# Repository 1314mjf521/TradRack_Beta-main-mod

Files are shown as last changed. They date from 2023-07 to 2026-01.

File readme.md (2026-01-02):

<!--
 * @Author: Mjf
 * @Date: 2023-06-24 20:04:52
 * @LastEditTime: 2024-05-12 15:53:49
 * @LastEditors: Win_VScode
 * @Description: 
 * @FilePath: \undefinedf:\download\TradRack_Beta-main\STLs\TradRack_Beta-main-mod\TradRack_Beta-main-mod\readme.md
 * 版权声明暂无
-->
# 以上MOD文件仅为测试使用用途，不得进行商用，不得进行商用，同时文件为开放式下载可进行转发及Fork但是不得商用售卖，一经发现拉黑，通告处理，源文件作者保留相关知识产权及法律诉讼通道，将提供文件归属权及开放时间证明！
## 仅仅是MOD文件不做解释全中文注释，有英文啥的不知道是啥随便看吧！  

# 本仓库仅为MOD文件不是完整文件，需要完整文件的自行找作者更新不解释原因  

中文TR-MOD解释用啥英文不可能得！！  

全套MOD不负责进行解释，搜集整理不会用别问我都是群友的自己去兔子群下载，高速下载衔接懒得放心情好了我在放！  
注意！！  
    在个别MOD文件中会有多个压缩文件，由于文件大小限制必须使用100M以下文件，所以进行打包！、

[TR公测地址](https://github.com/Annex-Engineering/TradRack)  
[TR开源衔接-国内加速](https://gitee.com/mjf521/TradRack)  
[动态网床使用-耗爹油](https://github.com/eamars/klipper_adaptive_bed_mesh)  
[动态网床使用-耗爹油-国内加速衔接](https://gitee.com/mjf521/klipper_adaptive_bed_mesh.git)  
[兔子垂直料架开源-耗爹油](https://github.com/eamars/VoronPrinterMods/tree/main/ercf_vertical_extrusion_stand)  
[兔子垂直料架开源-耗爹油-国内加速衔接](https://gitee.com/mjf521/VoronPrinterMods.git)  
[四色换色开源-唔，待定](https://github.com/feiwtyro/FEIW-multi_color)  
[四色换色开源-唔，待定-国内加速衔接](https://gitee.com/mjf521/FEIW-multi_color)  
[被动回卷-棒子开源](https://github.com/pure100kim/WinchRack_Type2)  
[龙头切刀](https://github.com/sorted01/Filametrix)  
[Voron2.4 换头-多头](https://github.com/viesturz/tapchanger)  
[双头 Voron2.4](https://github.com/FrankenVoron/Tridex)  
[木子小阳多色](https://github.com/muzixiaoyang/MZ-AMS-LITE-split-multi-color-3Dprint)  
[klipper_MMS](https://github.com/kingxuxu/AFC-Klipper-Add-On/tree/main)  
[BoxTurtle ](https://github.com/ArmoredTurtle/BoxTurtle)</p>
[国内玩家福利界面](https://video.majunfei.club/download_FULI.html)</p>
## 更新记录
###   2023-06-24 项目初步上传进行更新整理  
###   2023-06-25 更新自动回卷料架添加D轴支持  
###   2023-06-28 新增5.8L米桶支持，更新全套TR兔MOD，更新V3版6.3L米桶文件  
###   2023-06-29 大C套件更新，V5版电动回卷+V1版切刀+编码器等 
###   2023-07-01 更新被动回卷料架V2.0 更新全套MODV1.2  
###   2023-07-02 更新被动回卷料架V2. ,更新冷冷哒全套TR兔_MOD 1.4 ,新增小米空气净化器MOD-群友上传不做解释
###   2023-07-05 更新快乐兔配置文件（中文注释而已）， 更新基础屏幕教程，近期陆续更新快乐兔屏幕教程（更新中—）
###   2023-07-06 更新TR编码器-切刀-电动回卷-大C，新增20L被动回卷料架-葉
###   2023-07-09 新增20L被动回卷料架-唔，待定  更新大料盘适配
###   2023-07-10 更新TR编码器-切刀-电动回卷-大C-V3
###   2023-07-11 更新大佬动态网床初步测试中  
###   2023-07-14 更新20L被动回卷料架-V1-唔，待定，更新TR编码器-切刀-电动回卷-大C-V4  
###   2023-07-16 更新xiao主控配置文件中文注释进可以用来看中文注释不建议全抄，由于切刀问题个别参数不适合所有人  
###   2023-07-17 更新梦梦整理初版安装手册-V3持续更新中我懒别催,更新TR固定文件-政政的回忆录  
###   2023-07-18 更新ERCF-兔子垂直料架-耗爹油  
###   2023-07-19 新增4色开源项目-唔，待定，根据更新频率将文件压缩已完成，已完成文件向gitee得迁移加速    
###   2023-07-23 更新大C文件，同时更新安装文档（V5版本持续更新中） ，更新20L被动回卷料架-V3  
###   2023-07-27 更新安装文档（V6版本持续更新中）  
###   2023-07-30 更新TR型材固定-愚人方案V1， V7版安装教程初步完善    
###   2023-08-08 没事更新下檫料方案群友上传  ，更新V2快乐兔配置  
###   2023-08-17 更新大佬的FLY兔子板IO扩展板打板文件，更新木子小阳缓冲器（解决挤出不同步使用）  
###   2023-08-30 更新大C-6.3升电动回卷料架    
###   2023-08-31 更新V8安装说明只是更改一些错误</p>
###   2023-09-16 更新开源主板，原版Xiao+RP2040 双板子免费立创打板使用，至于零件如果不追求极致体验，原版兔子板的零件就能用</p>
###   2023-09-24 更新RP2040-zero开源主板新增热敏及7.2V电源输出接口（不要问为啥）</p>
###   2023-09-24 更新5.8L被动回卷料架</p>
###   2023-09-29 更新RP2040-zero开源主板，更新大佬龙头切刀</p>
###   2023-10-02 大C切刀文件更新阀门，RP2040主板全引脚引出添加7.2V及热敏接口，抛弃电动回卷及风扇接口</p>
###   2023-10-09 RP2040主板全引脚引出添加7.2V及热敏接口，抛弃电动回卷及风扇接口，增加全引脚主板测试中,微调can电路完成can引脚使用</p>
###   2023-10-14 RP2040主板引脚及电路测试完成，虽然无法共享UART引脚但是谁让2040引脚多呢随便玩，开源自行下载</p>
###   2023-10-17 RP2040主板新增全贴片方案，GPIO引脚丝印完善,更新20L料架</p>
###   2023-10-21 更新下快乐兔V2配置文件，自行根据所选主板完成配置及可建议只抄引脚剩下的自己慢慢对，已经帮你翻译过了</p>
###   2023-10-22 更新大佬被动回卷-木子小阳</p>
###   2023-10-28 更新TR升级兔子通道文件-☜♥☞鹏仔☜♥☞</p>
###   2023-10-29 tinysb切刀-适配N20切刀-数位星河</p>
###   2023-11-01 更新最新快乐兔配置文件，直客借阅不可照抄</p>
###   2023-11-10 更新大C电动回卷方案，计划更新V27套件包及快乐兔V2调试教程中文翻译</p>
###   2023-11-15 更新兔板引脚，同时完善前期问题更新1.5测试板及1.5.1测试板，更新V9版教程</p>
###   2023-12-02 更新大C光栅编码器，增加TR/TR兔安装文件</p>
###   2023-12-10 更新大C光栅编码器，更新数位星河-tinysb切刀</p>
###   2023-12-16 更新1.5.2打板文件外壳文件</p>
###   2023-12-23 更新TR中文文件下载地址,作者已开放公测，文件开始正常下载，中文文件下载地址位于安装手册中自行寻找</p>
###   2024-01-13 日常更新TR-MOD，文件较多不再具体描述，更新兔子板文件，更新MOD文件</p>
###   2024-05-11 日常更新TR-MOD，文件较多不再具体描述，更新兔子板1.6.2文件</p>
###   2024-05-12 更新兔子板贴片问文件同时更新相关介绍及引脚</p>
###   2024-05-29 更新断头V6切刀文件，无需截断刀片，4号刀片直接使用</p>
###   2024-07-07 更新兔子版文件，更新TR-Blink打印件（P站下载）</p>
###   2024-10-06 更新兔子屏幕汉化包，优化相关BUG，更新大C 3.1版本切刀，Voron2.4龙门擦嘴滑梯-胖松鼠</p>
###   2024-10-26 更新全新Klipper_MMS(klipper_ams)开源软件地址,BoxTurtle地址</p>
###   2026-01-02 新年没事把前面测试完成的STM32板子更新下</p>

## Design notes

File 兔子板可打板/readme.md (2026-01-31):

<!--
 * @Author: Mjf
 * @Date: 2023-09-16 18:54:57
 * @LastEditTime: 2024-05-12 13:33:59
 * @LastEditors: Win_VScode
 * @Description: 
 * @FilePath: \undefinedf:\download\TradRack_Beta-main\STLs\TradRack_Beta-main-mod\TradRack_Beta-main-mod\兔子板可打板\readme.md
 * 版权声明暂无
-->
### 梦梦专属兔子板V1.3
**原版xiao已做验证可正常使用，RP2040主板已验证**  

算了我补下零件清单吧
> 1、XH2.54  3-4P 插座（2040需要买点2P的）  
2、2P，7P-8P引脚（2.54单排母-2040需要9P跟5P的）  
3、独石电容0.33UF，0.1UF   
4、KF127-5.08 2P直插（电源输入-觉得不方便的自己换）  
5、10K色环电阻 其实每张板子就用4个（2040需要其它电阻的，另外就是0R贴片自己换导线）  
6、L7805CV电源转换（可换成5V1A或是5V3A模块不值钱自己换）  
7、直插电解电容25V100UF（白菜价）  
8、UART跟保护电阻啥的买个锤子直接烙铁焊接完事  
9、120欧 色环电阻（can板保护电路-2040专用）  
10、0欧贴片保护电阻（买个锤子-2040专用）  
11、100NF贴片电容（保护作用不要没啥事-2040专用）  
12、30PF贴片电容（保护作用不要没啥事-2040专用）  
13、CJ3400 SOT-23 场效应管  （4个扩展电路使用-2040专用）  
14、主控Seeduino Xiao  35一个随便买、RP2040-zero 超过15不要买  
15、单排排针买40个绝对用不完  

*xiao-兔子板引脚配置如下自行验证:*
>   G-EN PA2  
    G-STEP PA4  
    G-DIR PA10  
    S-EN PA11  
    S-STEP PA9  
    S-DIR PB8  
    UART PA8  
    SERVER1 PA6  
    SERVER2 PA5  
    ENCODER PB9  
    ENDSTOP PA7  
# xiao-兔子板丝印:
xiao双舵机板丝印
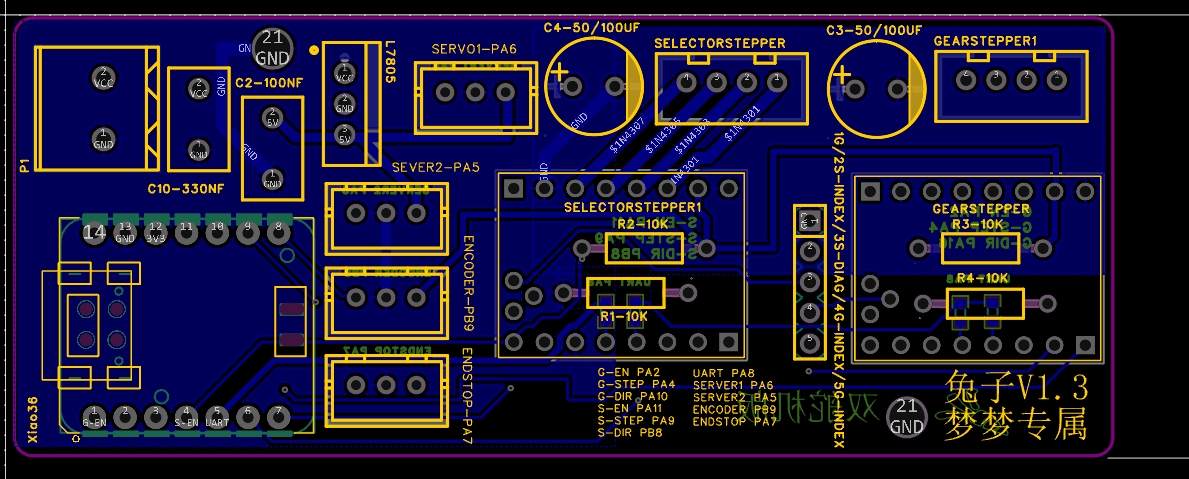
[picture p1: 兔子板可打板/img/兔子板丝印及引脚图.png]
丝印


# 所有UART引脚位置100R电阻可直接连接焊锡，也可以更换为其他阻值，但是不建议更改  
**RP2040-V1.2引脚(改线后)（使用UART引脚复用需给SELTETE驱动MS1短接3.3V电压）**
>S-DIR gpio0  
S-STEP gpio1  
S-EN gpio2  
S-EndStop gpio3  
G-DIR gpio4  
G-STEP gpio5  
G-EN gpio6  
G-EndStop gpio7  
UART gpio8 （sele 寻址用0 GEAR寻址用1 ）    
Fan1  gpio27  
Fan2 gpio26  
Rewinding1  gpio9（未改线为gpio29）  
Rewinding2 gpio28  
Temp gpio29（未改线为gpio9无法使用）  
Servo1  gpio14  
Servo2  gpio15  
CAN引脚定义  
RX gpio13  
TX gpio12  

**RP2040-V1.3全引脚（使用UART引脚复用需给SELTETE驱动MS1短接3.3V电压）** 
>S-DIR gpio0  
S-STEP gpio1  
S-EN gpio2  
S-EndStop gpio3  
G-DIR gpio4  
G-STEP gpio5  
G-EN gpio6  
G-EndStop gpio7  
UART gpio8 （sele 寻址用0 GEAR寻址用1 ）    
Temp gpio29（未改线为gpio9无法使用）  
Servo1  gpio14  
Servo2  gpio15  
CAN引脚定义  
RX gpio13  
TX gpio12  

**RP2040-V1.4.2全贴片**
>S-DIR gpio0  
S-STEP gpio1  
S-EN gpio2  
S-EndStop gpio3  
S-UART gpio8  
G-DIR gpio4  
G-STEP gpio5  
G-EN gpio6  
G-EndStop gpio7  
G-UART gpio10  
Fan1  gpio27  
Fan2 gpio26  
Rewinding1  gpio9  
Rewinding2 gpio28  
Temp gpio29    
Servo1  gpio14  
Servo2  gpio15  
CAN引脚定义  
RX gpio13  
TX gpio12  

**RP2040-V1.5.2/1.6.2引脚（使用UART引脚复用需给SELTETE驱动MS1短接3.3V电压）**
>S-DIR gpio0  
S-STEP gpio1  
S-EN gpio2  
S-EndStop gpio3  
~~S-UART gpio8  0  ~~
G-DIR gpio4  
G-STEP gpio5  
G-EN gpio6  
G-EndStop gpio7  
~~G-UART gpio8 1~~   
UART gpio8 （sele 寻址用0 GEAR寻址用1 ） 
Temp gpio29  
Servo1  gpio14  
Servo2  gpio15  
CAN引脚定义  
RX gpio13  
TX gpio12    

RP2040双舵机加can引脚图  
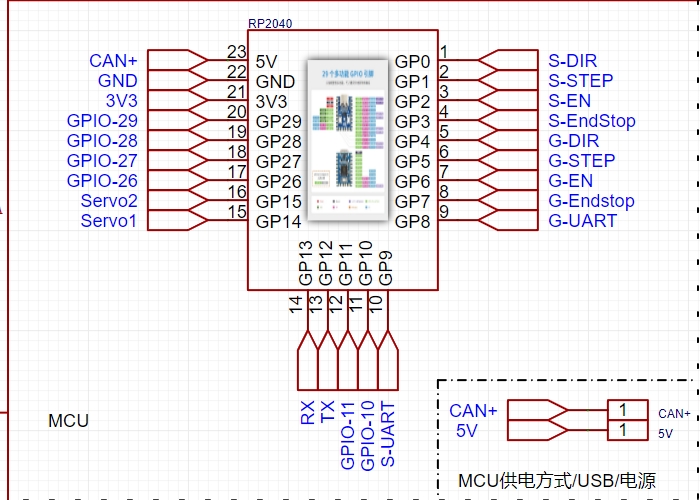
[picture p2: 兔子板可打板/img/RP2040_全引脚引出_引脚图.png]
  
RP2040双舵机加can正面  
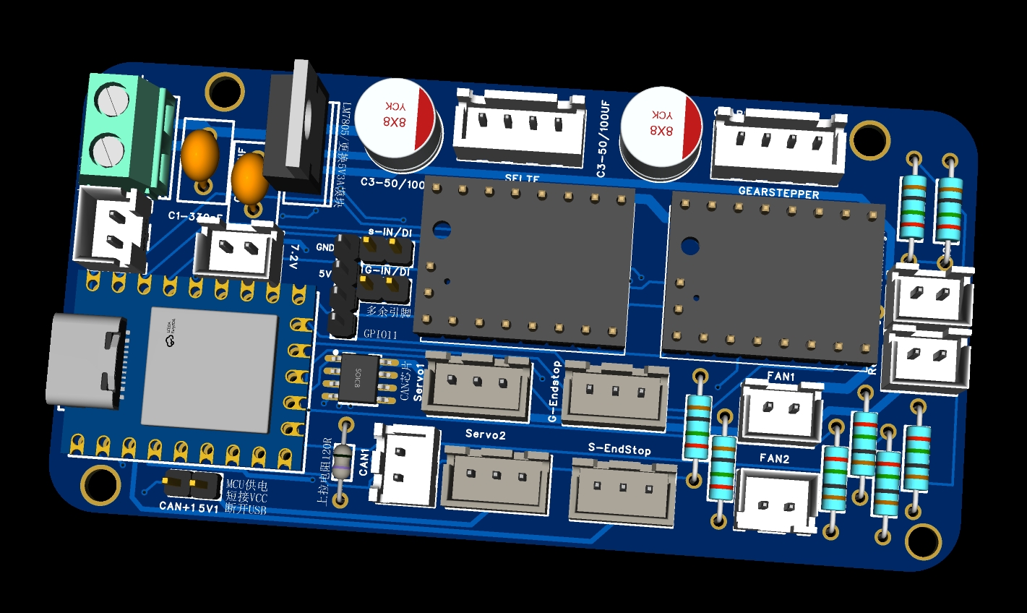
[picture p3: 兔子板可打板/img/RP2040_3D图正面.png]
  
RP2040双舵机加can背面  
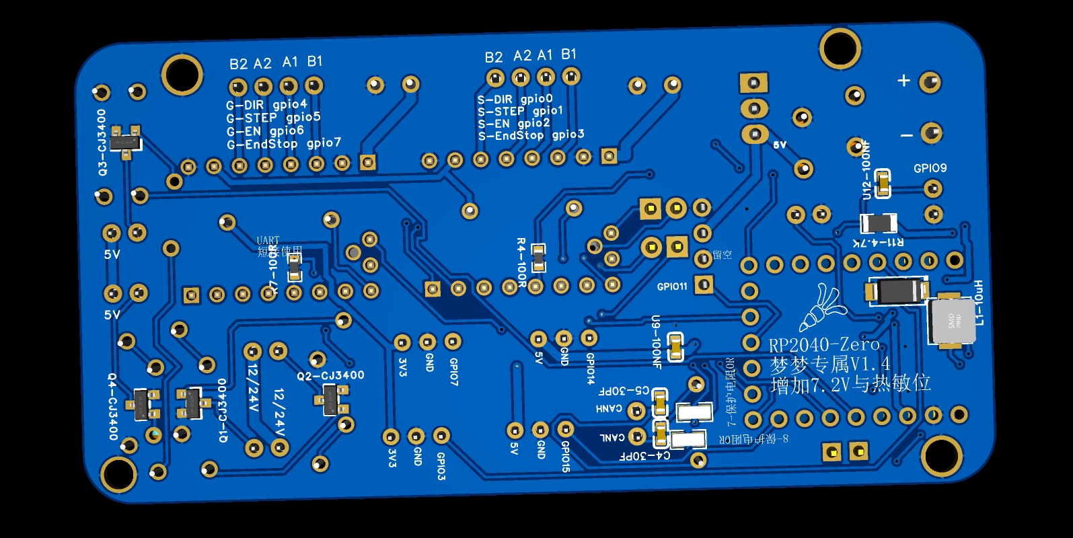
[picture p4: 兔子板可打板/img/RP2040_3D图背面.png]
  
RP2040双舵机加can引脚图全引脚引出  
  
RP2040双舵机加can引脚图全引脚引出正面  
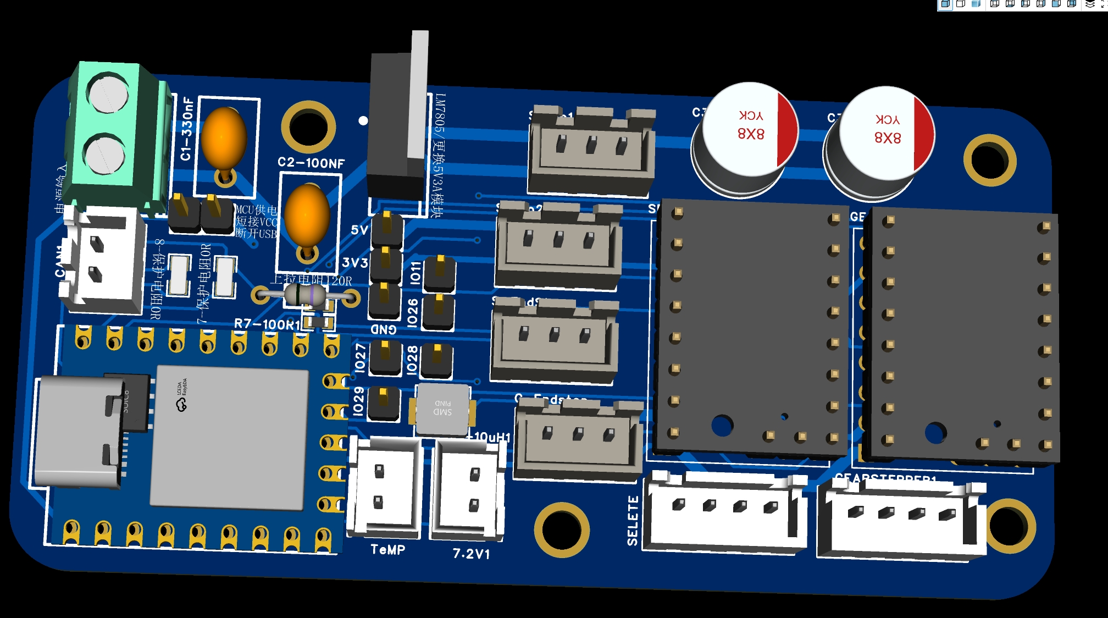
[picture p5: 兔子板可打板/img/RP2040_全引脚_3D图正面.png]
 
RP2040双舵机加can引脚图全引脚引出背面  
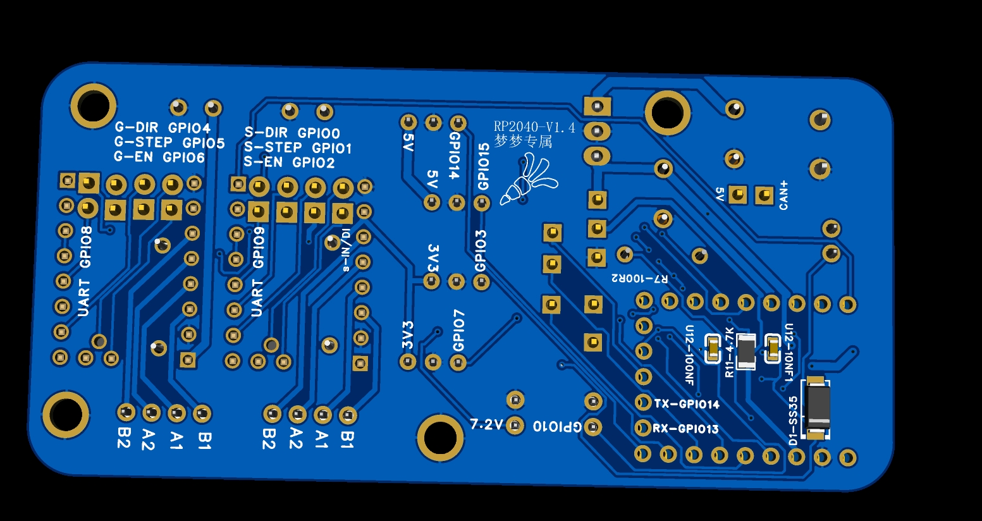
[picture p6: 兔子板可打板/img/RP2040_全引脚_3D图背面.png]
 
RP2040贴片双舵机加can引脚图  
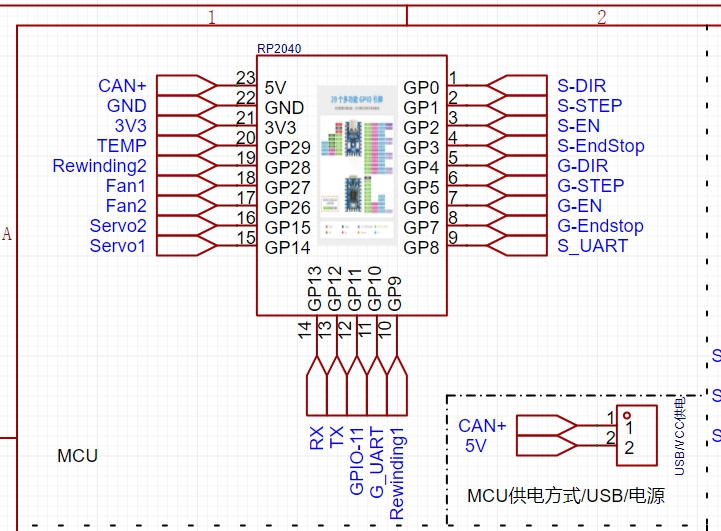
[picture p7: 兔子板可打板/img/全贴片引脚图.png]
 

# 1.6.2主板全图  
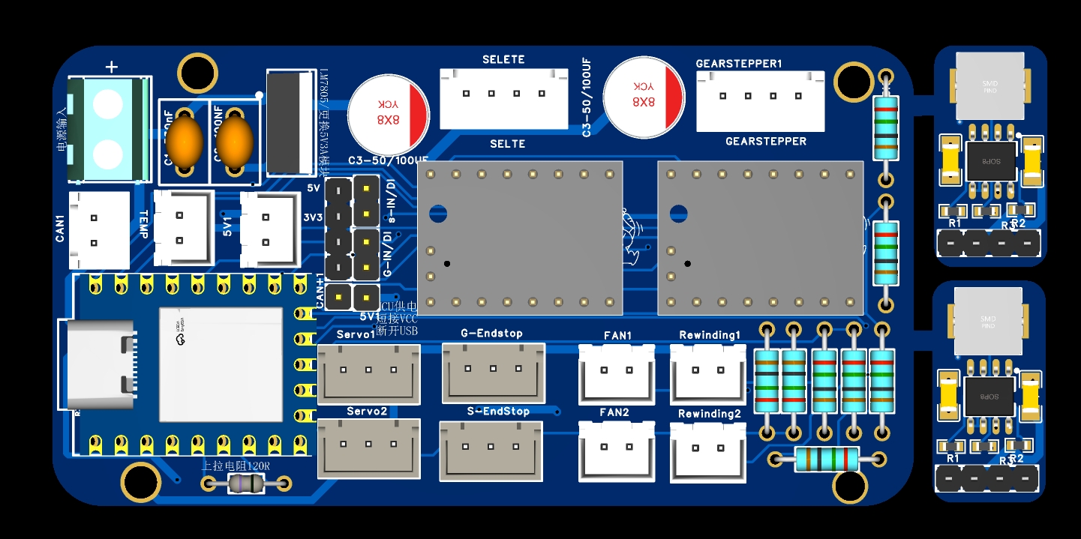
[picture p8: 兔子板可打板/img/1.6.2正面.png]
  
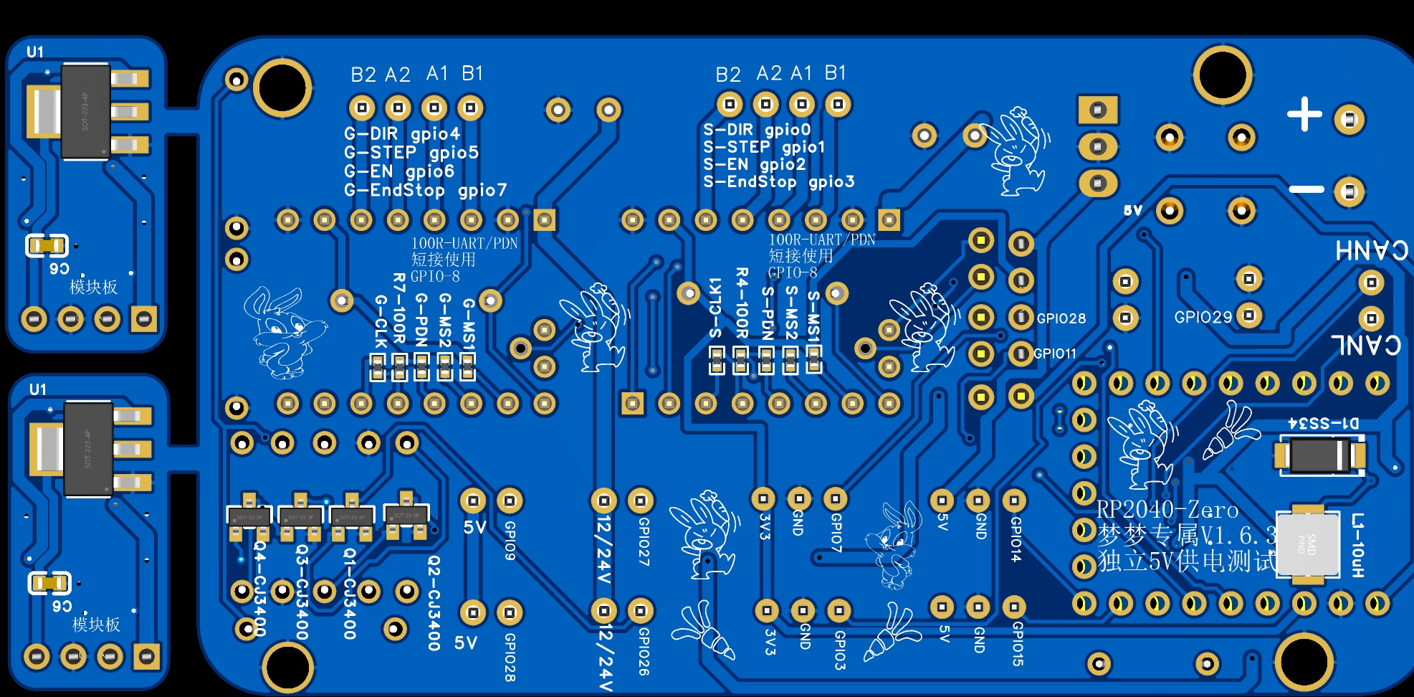
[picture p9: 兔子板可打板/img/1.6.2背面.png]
   
# 贴片主板全图  
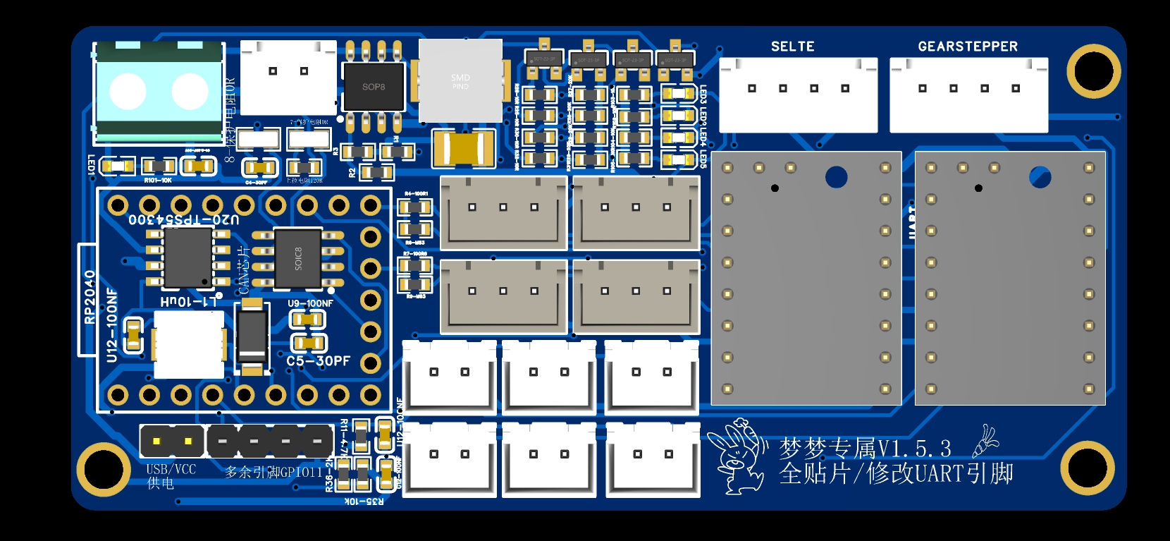
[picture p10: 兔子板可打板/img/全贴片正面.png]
  
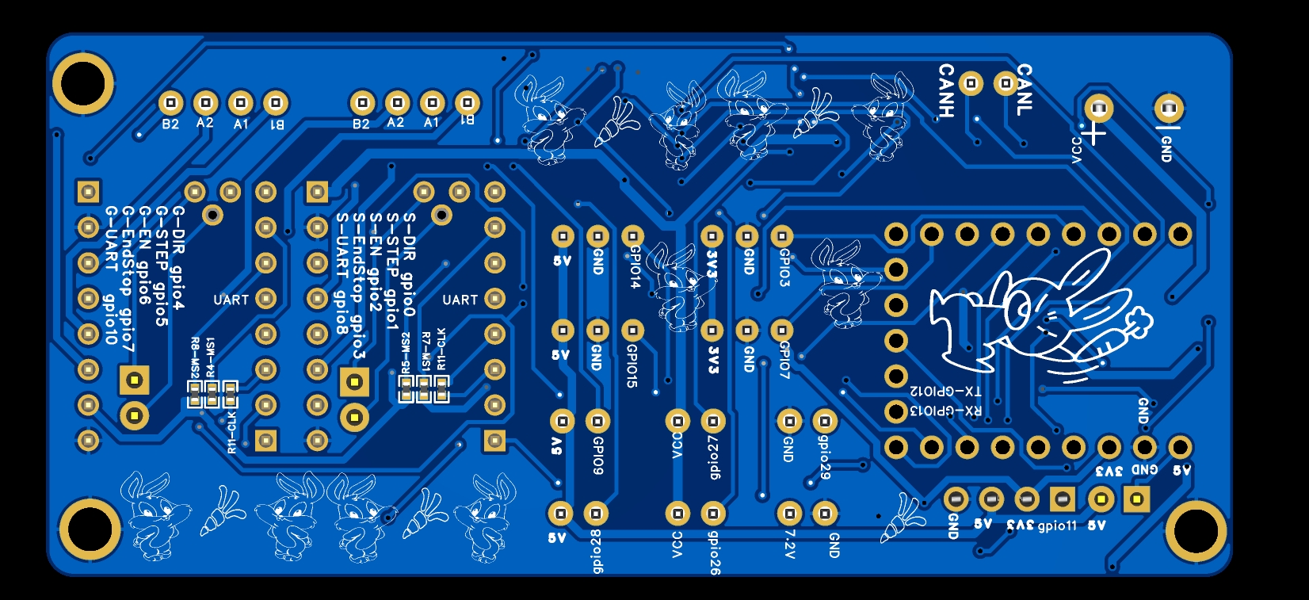
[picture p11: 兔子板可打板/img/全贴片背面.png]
 
# 新增拼板文件
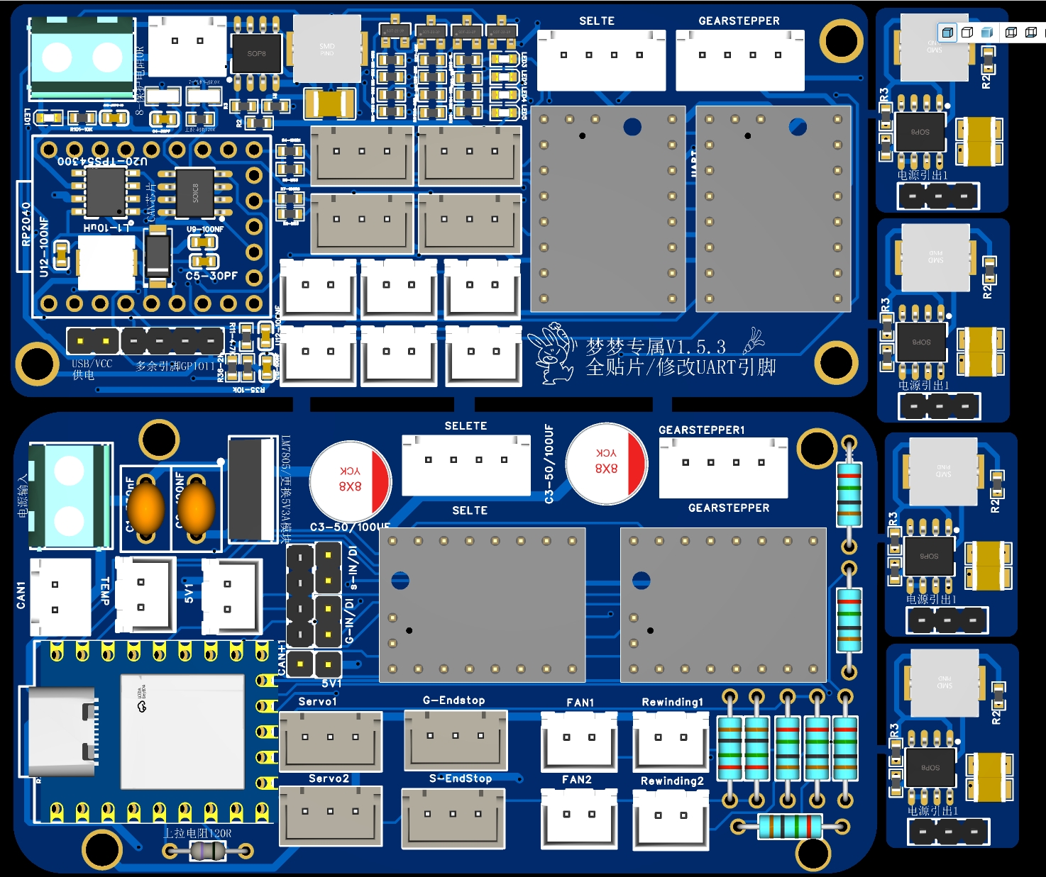
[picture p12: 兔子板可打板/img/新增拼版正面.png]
新增拼版正面

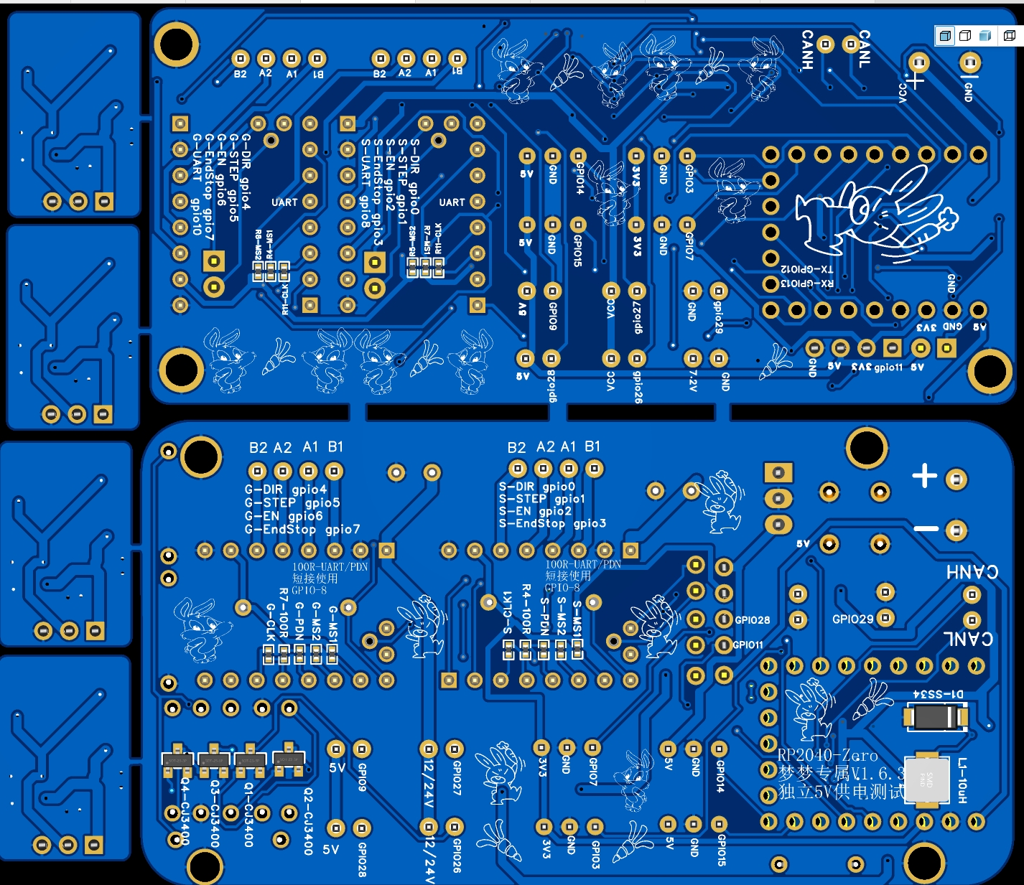
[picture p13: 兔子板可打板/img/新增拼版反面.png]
新增拼版背面


# STM32 主板双版本
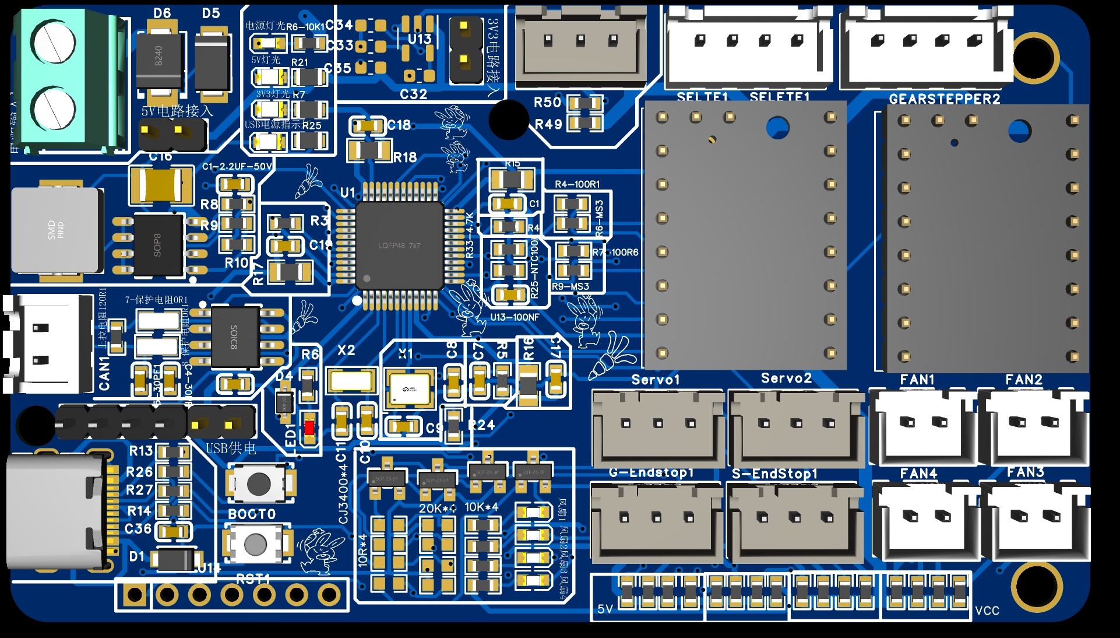
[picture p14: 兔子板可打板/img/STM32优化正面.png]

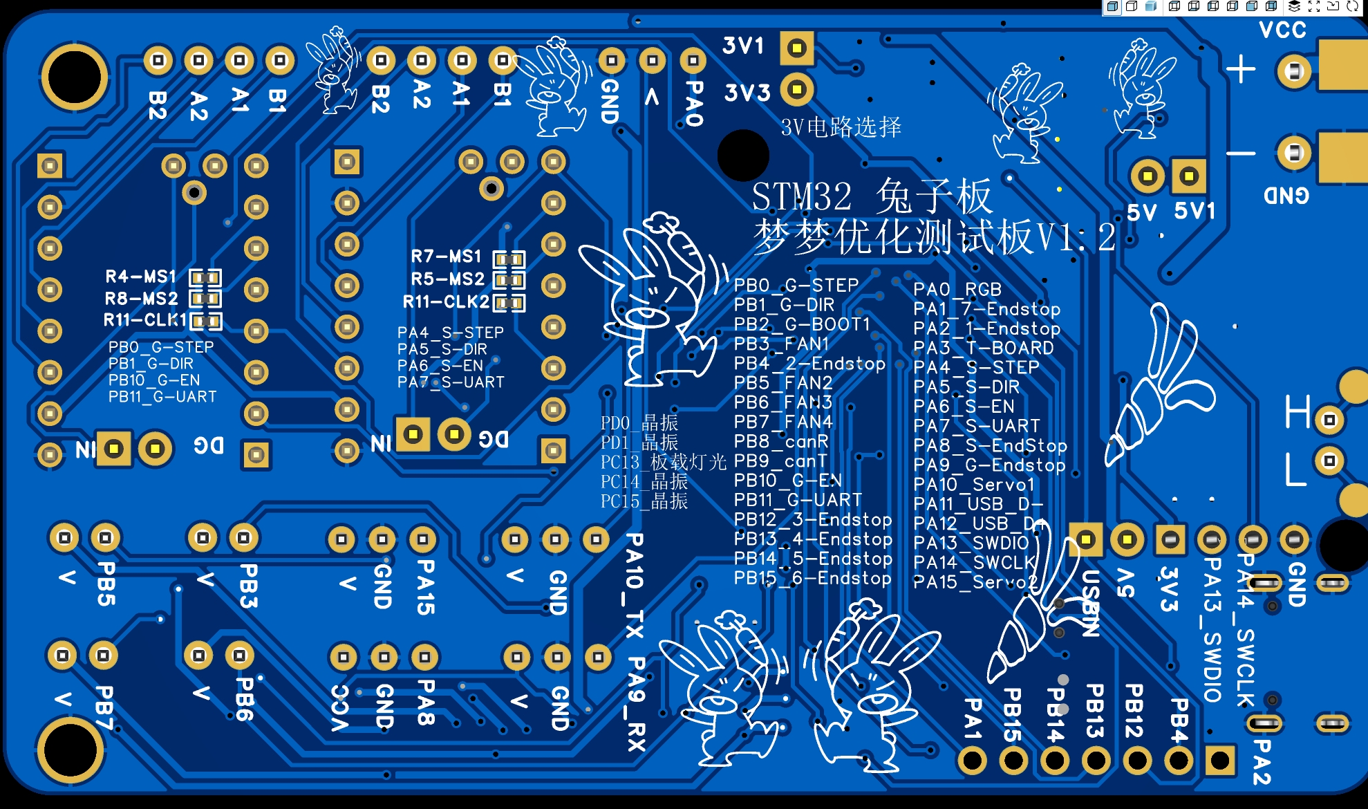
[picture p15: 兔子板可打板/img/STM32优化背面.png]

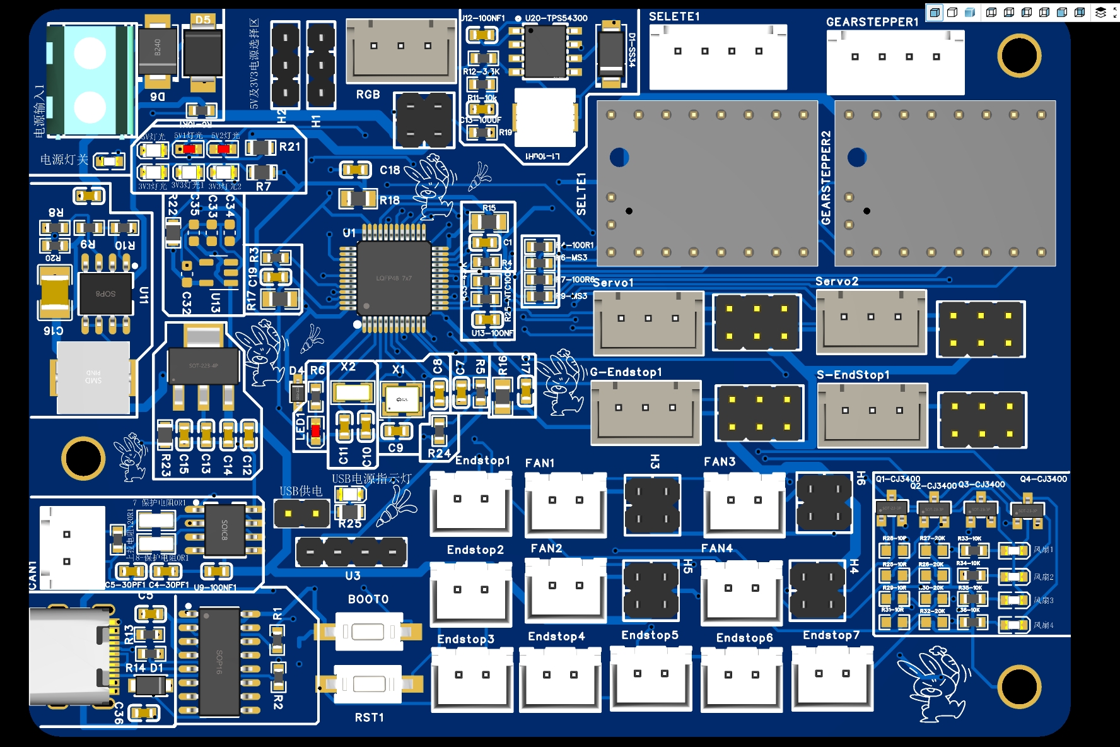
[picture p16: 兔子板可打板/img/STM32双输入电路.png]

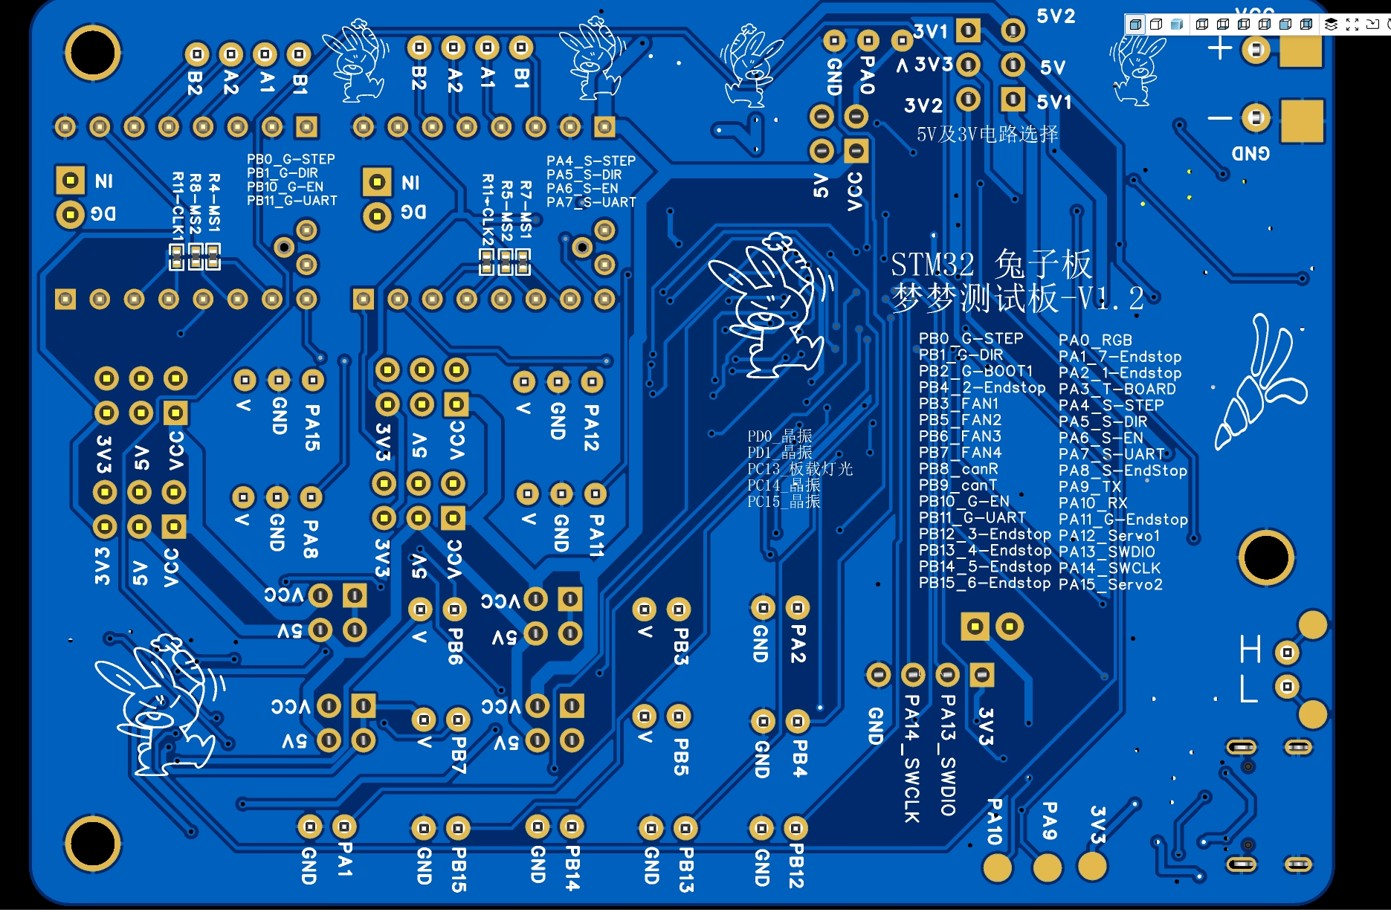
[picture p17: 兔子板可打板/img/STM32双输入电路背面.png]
  
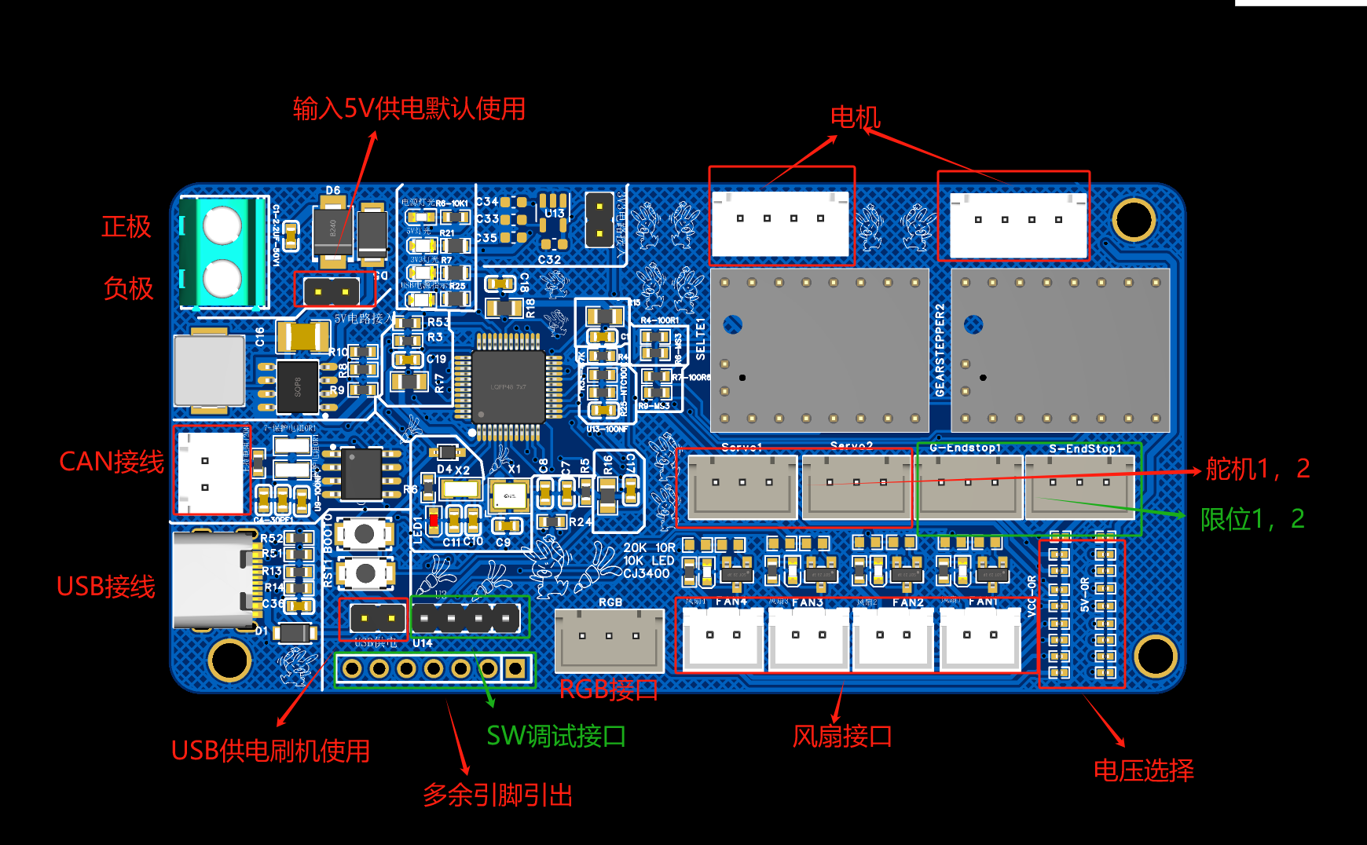
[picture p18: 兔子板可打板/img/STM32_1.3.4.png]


##  2023-09-24 RP2040-zero更新新增7.2V及热敏电阻位置不要问为啥因为我还没验证  
##  2023-09-29 RP2040-zero-V1.3原版存在UART无法使用，风扇电路短路问题，修改文件更改UART模式  

##  2023-10-09 RP2040-zero-V1.3修改封装类型，增加全引脚主板测试中,增加USB供电电路方便can使用     
##  2023-10-14 RP2040-zero-V1.4引脚测试完成开源使用，全文件共享附带焊接辅助,下一步目标拼板    
##  2023-10-17 RP2040-zero-V1.4引脚测试完成开源使用，新增全贴片方案，逐步修改丝印完善引脚图中，增加光污效果   
##  2023-10-17 RP2040-zero-V1.4纯粹完善丝印  
##  2023-11-15 RP2040-zero多个版本引脚完善，同时新增V1.5测试板（已知问题热敏位引脚不支持ADC模式，进一步优化进行优化预计发布V1.6版本  
##  2023-11-15 RP2040-zero多个版本引脚完善，同时新增V1.2合宙测试板
##  2023-11-16 RP2040-zero1.5.2更新外壳文件  
##  2024-05-12 RP2040-zero 1.6.2 版本更新，同时增加新版全贴片主板   
##  2024-06-16 RP2040-zero 1.6.2 贴片版本优化，新增合宙RP2040主板布局（暂时没时间截图就不放了）  
##  2024-07-07 RP2040-zero 1.6.2 贴片版本优化，新增合并版本文件，并完成相关验证，疯狂叠加电源板（不想买2.5的DCDC板可以自行购买零件）   
##  2024-07-21 STM32兔子版上线，成本20以内搞定还带主控,支持兔二9限位加上1个RGB接口,该拼版就拼版不要犹豫

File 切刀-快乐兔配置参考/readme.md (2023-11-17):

<!--
 * @Author: Mjf
 * @Date: 2023-07-19 20:39:04
 * @LastEditTime: 2023-11-17 18:42:59
 * @LastEditors: Win_VScode
 * @Description: 
 * @FilePath: \undefinedf:\download\TradRack_Beta-main\STLs\TradRack_Beta-main-mod\TradRack_Beta-main-mod\切刀-快乐兔配置参考\readme.md
 * 版权声明暂无
-->

1、修改V1快乐兔py文件2523行，添加或是删除切刀代码 （锁定关键代码：def _form_tip_standalone）<br/>
>''self.gcode.run_script_from_command("FILAMENT_CUTTING")''<br/>

2、修改兔子配置文件parking_distance值大小（新版本已更改无需手动改）<br/>
    **parking_distance: 43.0**  # 控制灯丝停放到栅极垫圈的距离（与编码器的距离，范围=12-30）<br/>
3、快乐兔升级注意<br/>
&emsp;新版快乐兔增加了电机同步py，使用升级时需要将新文件拷贝指<br/>
&emsp;&emsp;&emsp;/home/用户名/klipper/klippy/extras<br/>
&emsp;软衔接制作<br/>
&emsp;&emsp;**ln -s /home/用户名/ERCF-Software-V3/extras/manual_extruder_stepper.py /home/用户名/klipper/klippy/extras/manual_extruder_stepper.py**<br/>
4、快乐兔V3版本的挤出电机改名了！需要注意  
5、新增xiao配置中文注释翻译，由于自用切刀文件不可抄配置，参考中文注释即可   
6、~~针对新版快乐兔V2代码，print.cfg中挤出机中TMC配置全部删除剪切至快乐兔文件夹~~  
7、快乐兔V2全新方式完成安装后，针对切刀代码放置于  
>**/config/mmu/base/mmu_software.cfg** 

位置位于 
>**[gcode_macro _MMU_CUT_TIP]** 

同时修改 
>**/config/mmu/base/mmu_parameters.cfg** 

 >**form_tip_macro: _MMU_CUT_TIP**   # 切刀代码

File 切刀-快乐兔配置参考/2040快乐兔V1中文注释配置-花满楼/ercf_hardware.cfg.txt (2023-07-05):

##愤怒的兔子：Carrot Feeder配置文件，带有｛brd_type｝mcu的配置
##
##EASY-BRD安装说明：
##J6跳线设置：
##选项1：引脚2-3和4-5，即。[..][..]
##这是用于无传感器选择器设置。请注意，这将启用选项，禁用“额外”
##开关，以便刀头传感器（如果使用）必须连接到主mcu
##选项2：引脚1-2和4-5，即[..].[..]
##如果你没有使用无传感器选择器。“额外”开关可用于其他用途
##
##Fysetc Burrows再培训局设置说明：
##此板上不需要跳线配置，但已连接12v/24v电源
##固件安装：
##>制作菜单配置（rpi2040，无引导加载程序）
##>制造
##将卡置于引导加载程序模式：按住“BOOTSEL”；单击“重新设置”；释放“BOOTSEL”
##>使闪光flash_DEVICE=2e8a:0003

##
##
[mcu ercf]
serial: /dev/serial/by-id/usb-Klipper_rp2040_CB6190905B153D30-if00

#####################  挤出电机配置  #############################

[tmc2209 manual_stepper gear_stepper]
uart_pin: ercf:gpio8 
uart_address: 0                 # uart 地址
interpolate: false
run_current: 0.8			
hold_current: 0.2			
sense_resistor: 0.110
stealthchop_threshold: 0		# 静音阈值

[manual_stepper gear_stepper]
step_pin: ercf:gpio4
dir_pin: ercf:gpio10
enable_pin: !ercf:gpio2
rotation_distance: 23.0191353		
gear_ratio: 50:17
microsteps: 32 				# 细分
full_steps_per_rotation: 200		# 脉冲数
velocity: 100
accel: 1000

#####################  选料电机配置  #############################
[tmc2209 manual_stepper selector_stepper]
uart_pin: ercf:gpio8
uart_address: 1
run_current: 0.8		
hold_current: 0.4		
interpolate: false
sense_resistor: 0.110
stealthchop_threshold: 9999	
#diag_pin: ^{selector_diag_pin}		# Set to MCU pin connected to TMC DIAG pin
#driver_SGTHRS: 75		# 灵敏度 0~255

[manual_stepper selector_stepper]
step_pin: ercf:gpio9
dir_pin: !ercf:gpio18
enable_pin: !ercf:gpio11
rotation_distance: 40
microsteps: 16 			
full_steps_per_rotation: 200	
velocity: 500
accel: 1000
#endstop_pin: tmc2209_selector_stepper:virtual_endstop	# 虚拟限位
endstop_pin: ^ercf:gpio19			# 物理传感器

##########################  舵机配置  ################################
[ercf_servo ercf_servo]
pin: ercf:gpio5
maximum_servo_angle: 180
minimum_pulse_width: 0.00085
maximum_pulse_width: 0.00215

##########################  编码器配置  ################################
[ercf_encoder ercf_encoder]
encoder_pin: ^ercf:gpio6			# 参考配置EASY-BRD: ^ercf:PA6,    Flytech ERB: ^ercf:gpio22
encoder_resolution: 1.356852	    #  ERCF_CALIBRATE_ENCODER 校准选料模块出料传感器传感距离（推出500mm耗材反复5次 )
extruder: extruder		

# 高级设置，但用于自动堵塞检测模式。确保您理解Discord或在Discord上提问
desired_headroom: 8.0		# ERCF将试图保持的跳动余量（最接近ERCF触发跳动）
average_samples: 4		 # 上次测量的“阻尼”效应。值越高，表示clog_length的减少速度越慢

[filament_switch_sensor toolhead_sensor]
pause_on_runout: False		# 必须为 False
switch_pin: EBBCan: PB5

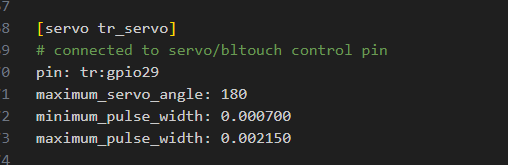
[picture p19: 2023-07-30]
117M舵机脉冲指南.png

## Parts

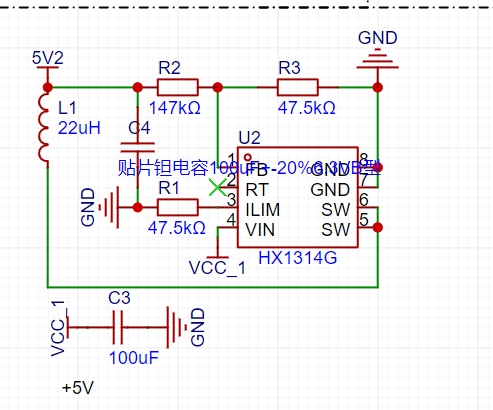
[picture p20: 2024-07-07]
兔子板可打板/img/电源板配件清单.png

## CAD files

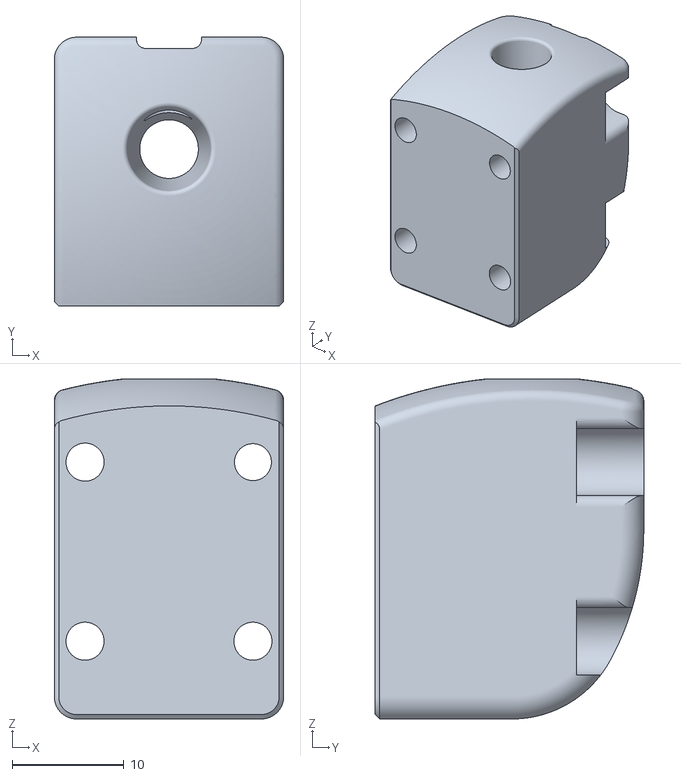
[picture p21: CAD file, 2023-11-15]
贯流风机固定文件-愚人/VORON2.4_Assembly_Z Bearing Block Bottom (3) v1.stl
20.5 x 24.0 x 30.4

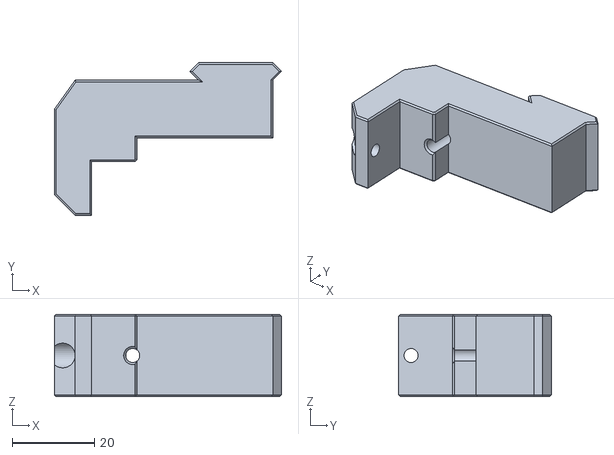
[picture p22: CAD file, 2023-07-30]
TR型材固定-愚人/固定5-直接打.STL
55.1 x 37.0 x 20.0

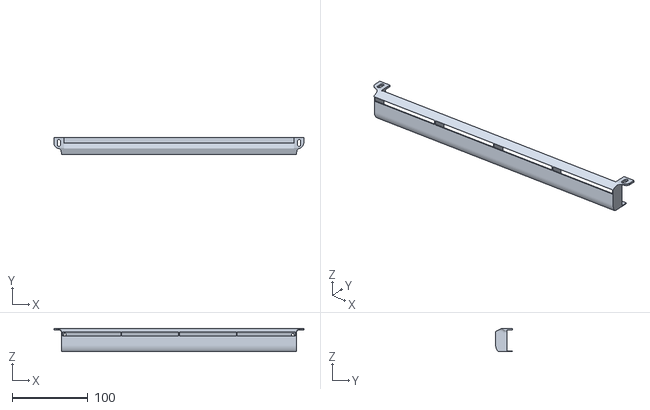
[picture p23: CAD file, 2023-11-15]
贯流风机固定文件-愚人/实体12.stl
330.0 x 22.0 x 31.0

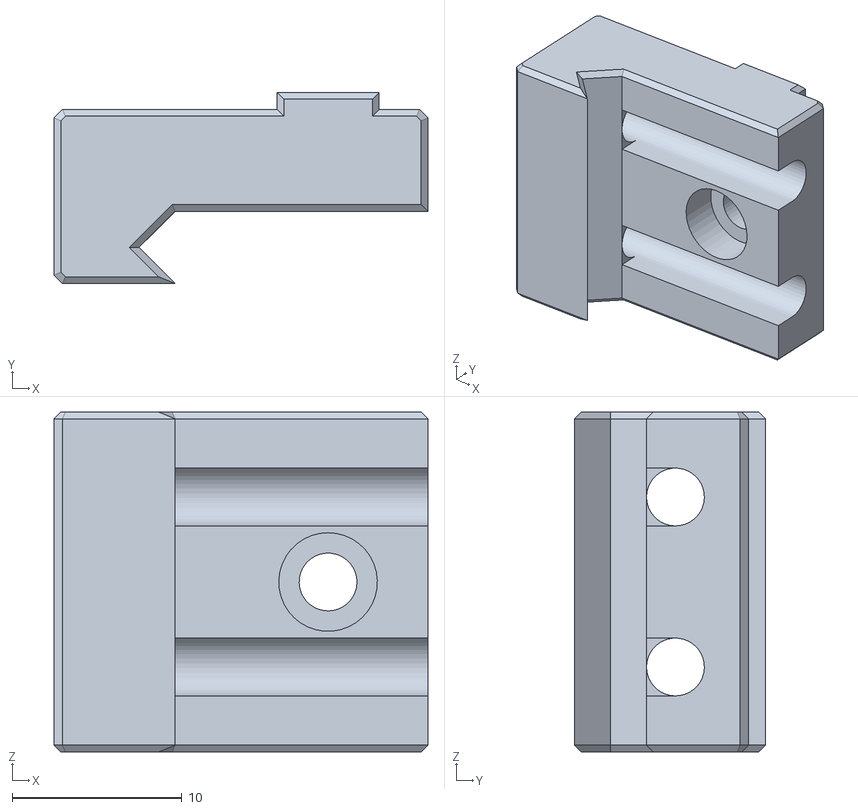
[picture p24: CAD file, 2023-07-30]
TR型材固定-愚人/固定3-直接打.STL
22.0 x 11.2 x 20.0

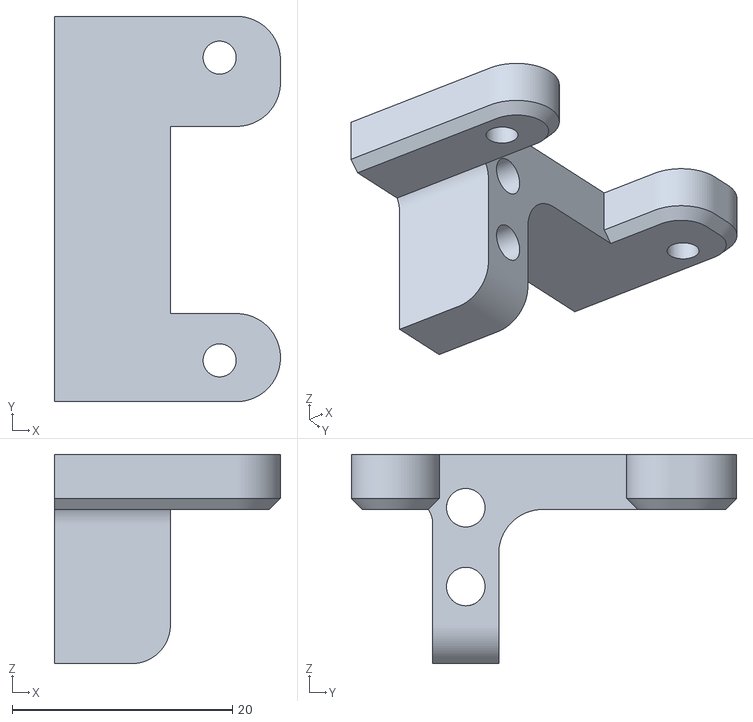
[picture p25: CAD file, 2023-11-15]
贯流风机固定文件-愚人/实体1.stl
20.5 x 35.0 x 19.0

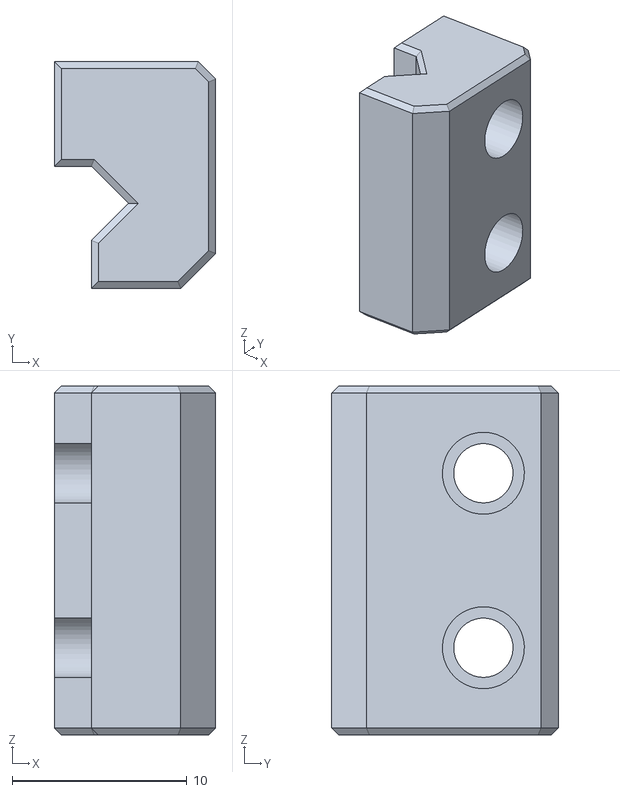
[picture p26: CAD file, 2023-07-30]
TR型材固定-愚人/固定1-直接打.STL
9.24 x 13.0 x 20.0

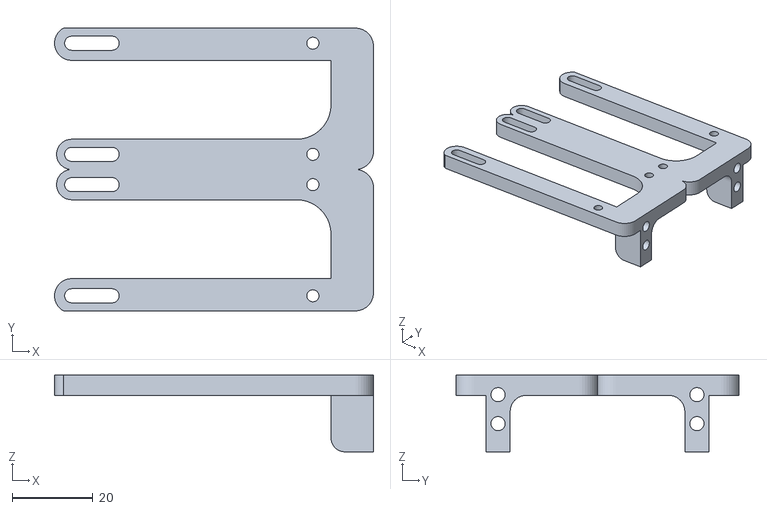
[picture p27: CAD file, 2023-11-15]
贯流风机固定文件-愚人/贯流安装组合图_零部件5 v3.stl
78.9 x 70.0 x 19.0

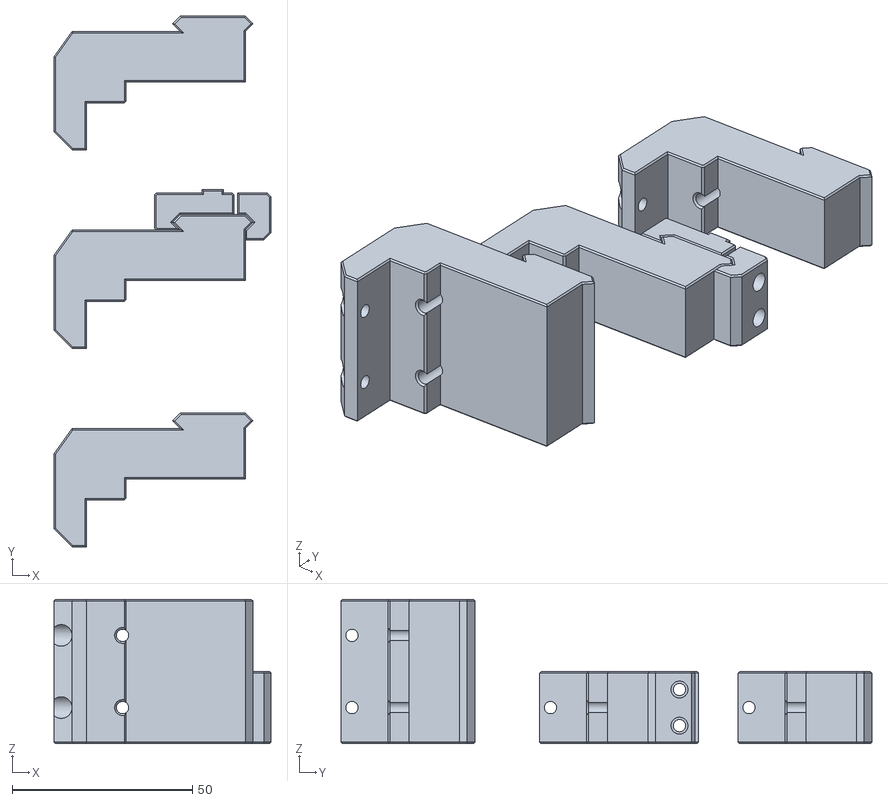
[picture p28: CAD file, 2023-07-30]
TR型材固定-愚人/tr支架for voron 5mm厚玻璃 直接打.STL
60.1 x 147.0 x 40.0

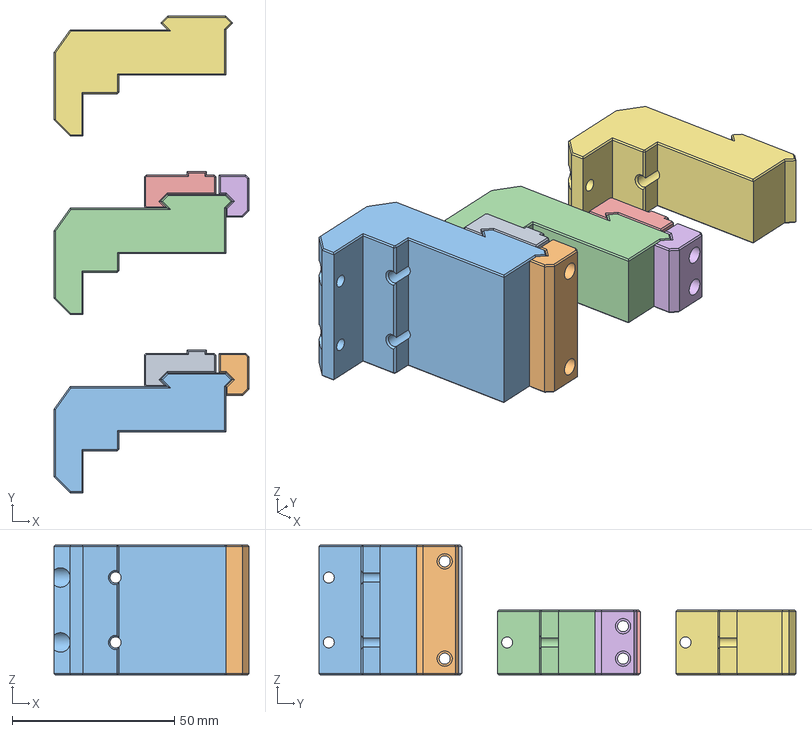
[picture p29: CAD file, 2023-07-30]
TR型材固定-愚人/tr支架for voron 5mm厚玻璃.step
60.1 x 147.0 x 40.0 mm

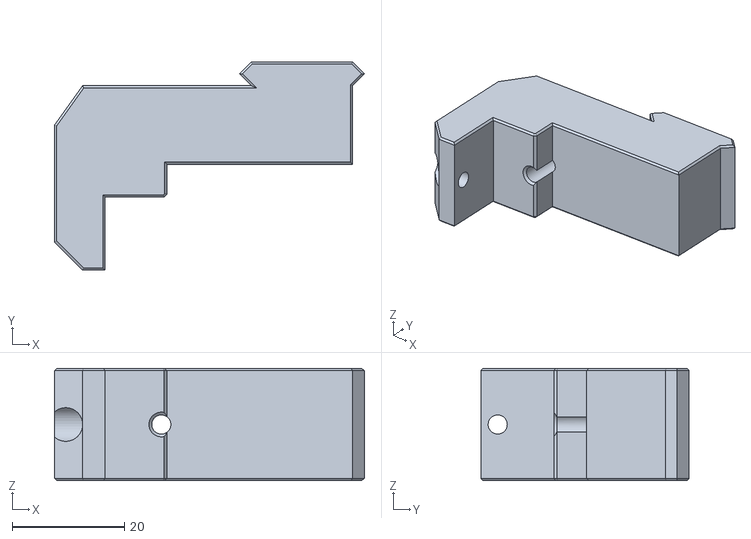
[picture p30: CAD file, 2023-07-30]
TR型材固定-愚人/固定2-直接打.STL
55.1 x 37.0 x 20.0

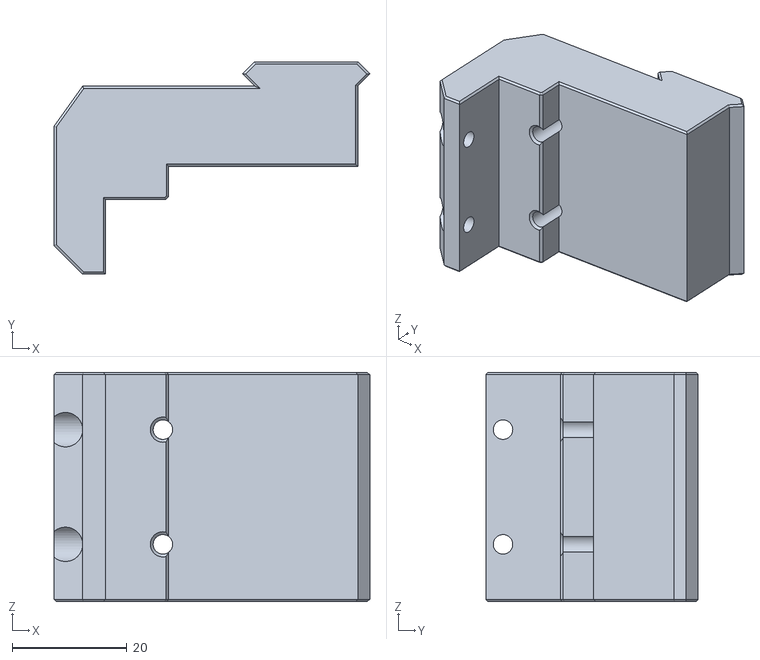
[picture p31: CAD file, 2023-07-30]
TR型材固定-愚人/固定4-直接打.STL
55.1 x 37.0 x 40.0

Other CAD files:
TR型材固定-愚人/输入4.SLDPRT
贯流风机固定文件-愚人/实体5.stl
TR型材固定-愚人/TR-1.SLDPRT
TR型材固定-愚人/输入2.SLDPRT
TR型材固定-愚人/输入5.SLDPRT
TR型材固定-愚人/输入3.SLDPRT
TR型材固定-愚人/输入1.SLDPRT
TR型材固定-愚人/tr支架for voron 5mm厚玻璃.SLDASM

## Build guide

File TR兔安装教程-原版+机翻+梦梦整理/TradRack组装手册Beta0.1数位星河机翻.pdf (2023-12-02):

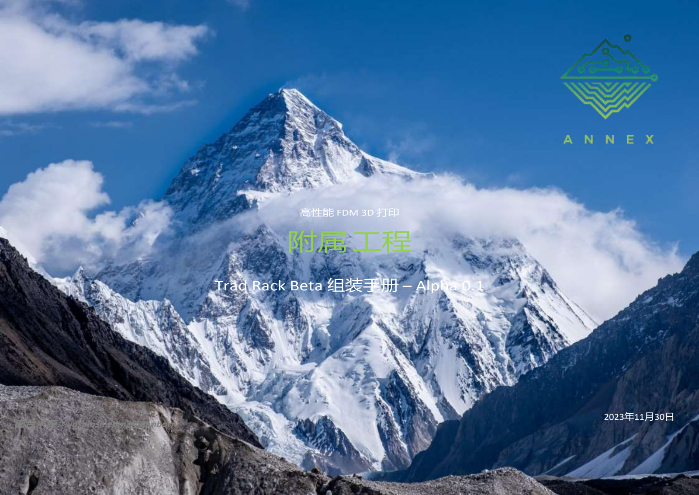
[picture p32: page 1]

### http://annex.engineering

1

### 高性能 FDM 3D 打印

# 附属工程

# Trad Rack Beta 组装手册 – Alpha 0.1

图片来源：unsplash.com/@danborn

### 2023年11月30日

## 关于我们

# 突破自制 3D 打印机的界限

附件工程是一个活跃在全球范围内的紧密团队，致力于各种项目组合。从挤出机到 床探测，从热端到运动系统，我们涵盖了这一切。我们运用流

体模拟、偏转分析以及系统和控制等真正的工程技能来充分利用我们的 设计。

我们 有 一个围绕Annex的 社区，可以在Discord上找到。

# 组装手册-目录

- 警告 | 04 | - 灯丝通道模块 | 46
- 介绍 | 05 | - 选择惰 轮端 | 51
- 常问问题 | 06 | - 腰带 | 54
- 概述 | 08 | - 电缆 盖 | 57
- 基本 框架 | 09 | - 电缆 链 | 60
- 选择器驱动端 | 15 | - 控制器 | 64
- 选择器模块 | 23 | - 制作人员 | 66
3

警告

- 电气 安全：

## 在你开始之前

仔细阅读并理解以下警告

- 在操作挤出机或任何电气组件之前，请务必 断开 电源并确保打印机 已关闭。_
- 遵循 正确的 接地 和 电气 安全 准则，以防止触电或事故。
- 维护和 清洁：
- 定期清洁 挤出 机 喷嘴和周围区域，以防止堵塞并保持最佳打印质量。
- 按照 制造 商的 说明 进行 正确的 维护程序 ， 例如润滑或更换磨损零件。
- 未能正确设置可能会导致火灾、爆炸、自毁或组件损坏。强烈建议在开始第一次打印之前进行手册中指定 的测试。_
- 在开始组装打印机之前，请考虑 阅读整本手册。
- 如需帮助，请咨询附件工程的适当渠道。
- 材料清单
- 推荐BOM中列出的项目 是有原因的。尽可能遵守它有助于防止过早或意外的失败。_
- 已经进行了广泛的 研究，以确保指定的零件满足我们对性能的期望。
- 使用正确的零件 可确保满意的维修间隔。

4

介绍

### 印刷零件指南

附件工程团队提供了一套打印指南供您遵守，以最大限度地提高打印零件的成功机会。虽然可能会有关于材料替代或印刷标准变更的询问，但我 们强烈建议遵循这些建议。提供的 STL 已经处于正确的方向。

### 制造类型

熔融沉积成型(FDM)

材料

作为一个

### 喷嘴尺寸

建议0.4或0.5mm

层高

0.1或0.2毫米

### 挤出宽度

0.4至0.5毫米

### 填充百分比

最小 40%（0.6mm 宽度时）

### 填充型

网格、螺旋体、蜂窝、三角形或立方体

墙数

最少3 个

### 实心顶层/底层

最少 5 个（0.2mm 高度）

5

# 常问问题

### 什么是 eDrawing？我该如何使用 它们？ eDrawings是一款软件应用

程序，允许用户查看项目的 3D 模型并与之交互。它在构建过程中充当有用的指 南。要使用 eDrawings，只需打开软件并加载 3D 模型文件即可。从那里，您可以导 航和探索模型、放大和缩小、旋转、测量尺寸，甚至进行注释。它提供了一种在施 工前和施工期间可视化和了解项目的便捷方法。

为什么没有针对product_x 的CAD 输出？

仅当产品达到“发布” 状态时，CAD 文件才可用于产品。这种方法使我们能够坚 持高标准的质量，并最大限度地减少那些选择分叉我们项目的重复工作的可能 性。

### 当附件发布源文件时，我们为什么不呢？

发布步骤文件而不是 parasolid？

在 CAD 领域，STEP 格式众所周知是有损的，因为它可能导致 曲面损坏和丢失 ， 从而导致模型不完整。另一方面，Parasolid文件是本机CAD文件，删除了特征树 以便于共享。这确保了最终用户体验到最接近的“原生体验”。

### 我应该购买 OEM 还是从速卖通购买？

建议从 Bondtech 采购 OEM 零件，而不是从速卖通购买克隆零件，因为它们具 有卓越的质量、兼容性和可靠的客户支持。

### 推荐使用什么类型的润滑油？

对于滚针轴承，建议仅使用锂基润滑脂。适量涂抹，防止灰尘和碎屑堆积。此 外，请确保避免接触塑料部件。切勿使用硅酮或 PTFE 基润滑剂，这一点至关重

要。

什么是VC3或VC125？

Vibra-Tite VC3或VC125是一种液体粘合剂，可防止紧固件因振动而松动。它提供 了牢固的粘合，并且易于拆卸而不会损坏组件。

### 我怎样才能获得更多帮助？

加入我们的 Discord： https: //discord.gg/MzTR3zE

6

# 扭矩参考表

扭转

为了保持机械组件的完整性和安全性，必须将螺栓正确拧紧到指定的扭矩值。这可以防止它们随着时间的推移而松动，从而导致潜在的故障或事 故。扭矩是指施加到螺栓上的旋转力的大小，通常以牛顿米 (Nm) 为单位。

参考扭矩 表时，请务必注意任何其他说明或建议。_ 有些页面可能会特别指出使用螺纹锁固剂，这种物质可以防止螺栓因振动或其他外力而 松动，从而帮助固定螺栓。螺纹锁固剂通常在拧紧之前涂在螺栓螺纹上。

公制螺栓尺寸 | 穿过材料A | 进入材料B | 扭矩（牛米）
M2 | 塑料 | 塑料 | 0.25
M2.5 | 金属 | 金属 | 0.4
M3 | 金属 | 黄铜嵌件 | 1
M3 | 塑料 | 塑料 | 0.4
M3 | 金属 | 金属 | 1
M5 | 金属 | 黄铜嵌件 | 0.4
M5 | 金属 | 金属 | 3
M5 | 金属 | 塑料 | 1
M5 | 金属 | 黄铜嵌件 | 3

提示

| 为了在组装过程中方便参考，可以打印此页。

。
7

# 传统机架 – 概述

8

# 基础框架-概述

9

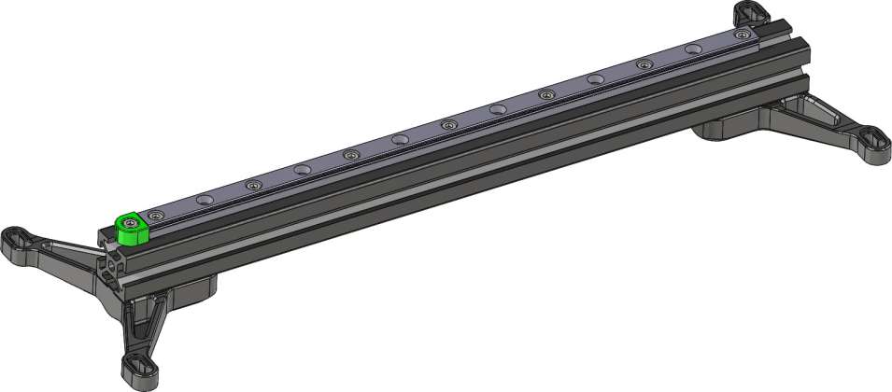
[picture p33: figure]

# 基架 -组装

2020 挤压

挤压

任何 T 型槽 2020 挤压件的备用件均可用于 Trad Rack。挤出时间越长，可以添加的细 丝通道就越多。参考计算器了解给定数量的长丝通道所需的最小长度。

根据Trad Rack的安装方式 ，使用比所需长度更长的挤压件可能会很有用。例如，建 议安装在K3侧面的最小长度为280mm 。
10

# 基架 -组装

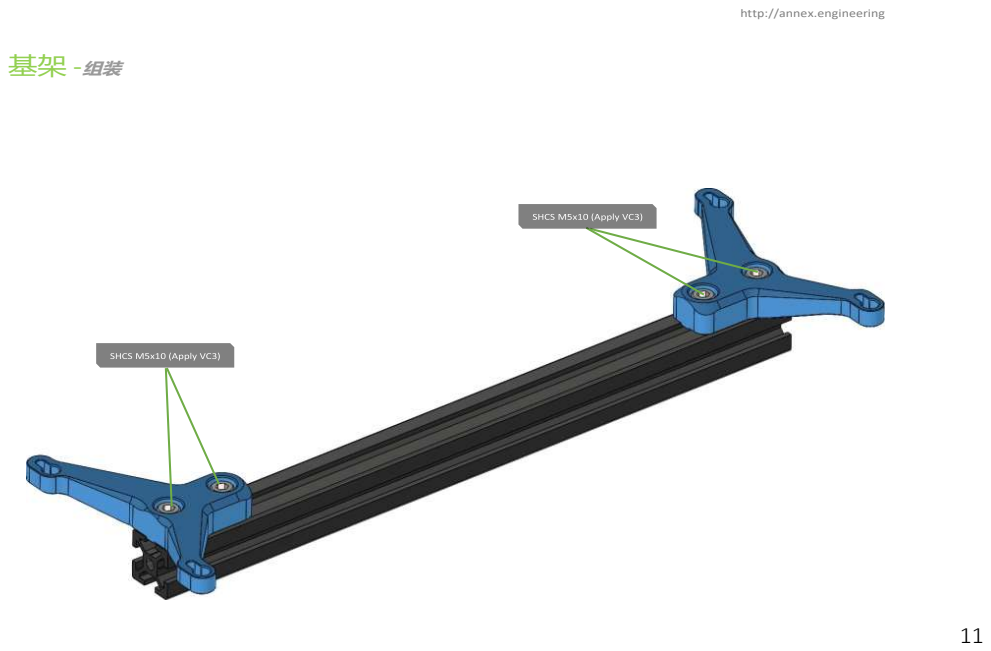
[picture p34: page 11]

# 基架 -组装

为了更方便的安装过程，请使用印刷的 MGN9 对齐工具。

# 基架 -组装

此页有意留为空白

14

# 选择器驱动端- 概述

15

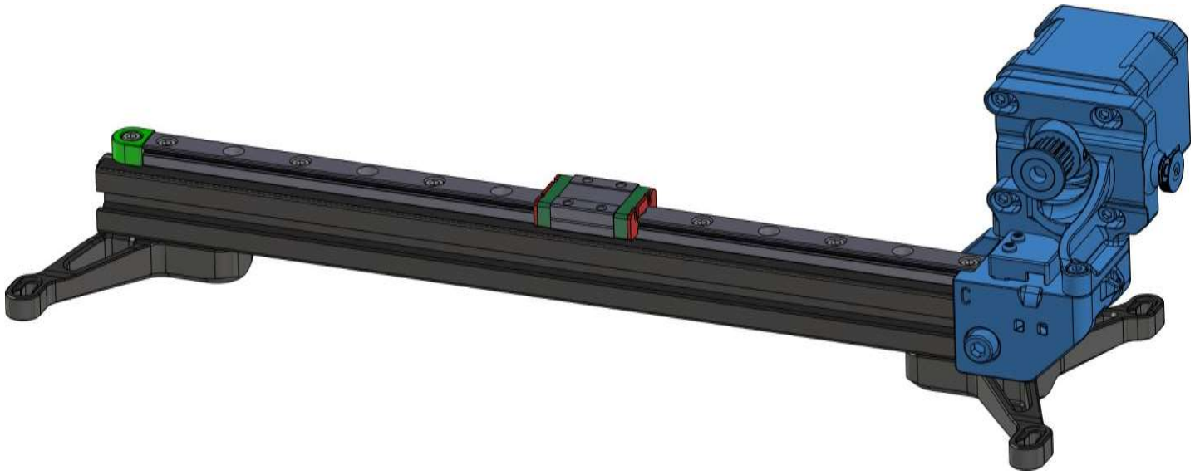
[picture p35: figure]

# 选择器驱动端 –装配

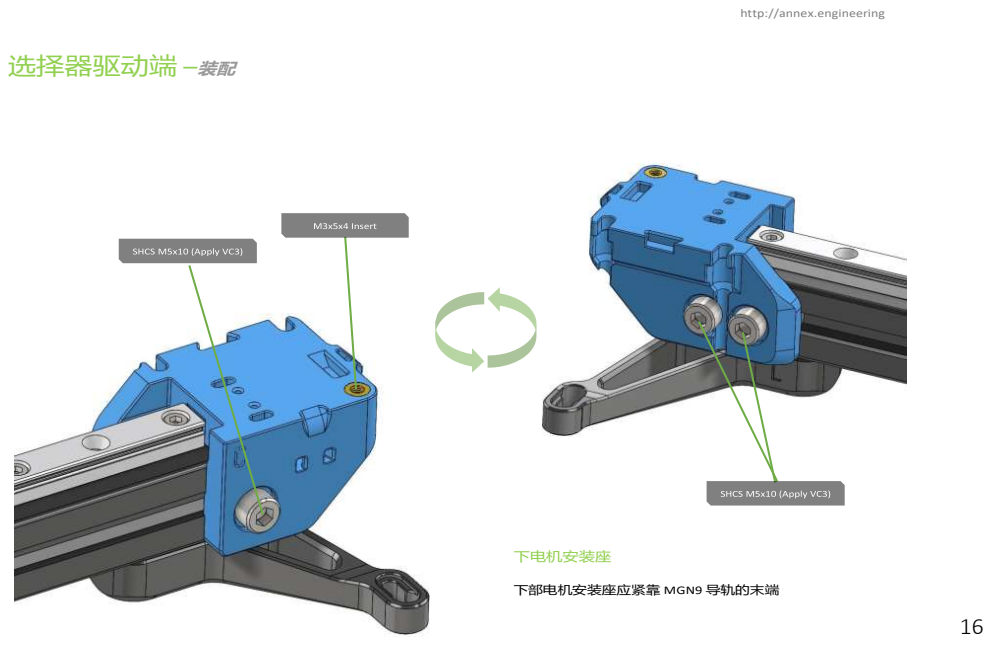
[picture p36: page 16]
下电机安装座; 下部电机安装座应紧靠 MGN9 导轨的末端

# 选择器驱动端 –装配

# 选择器驱动端 –装配

# 选择器驱动端 –装配

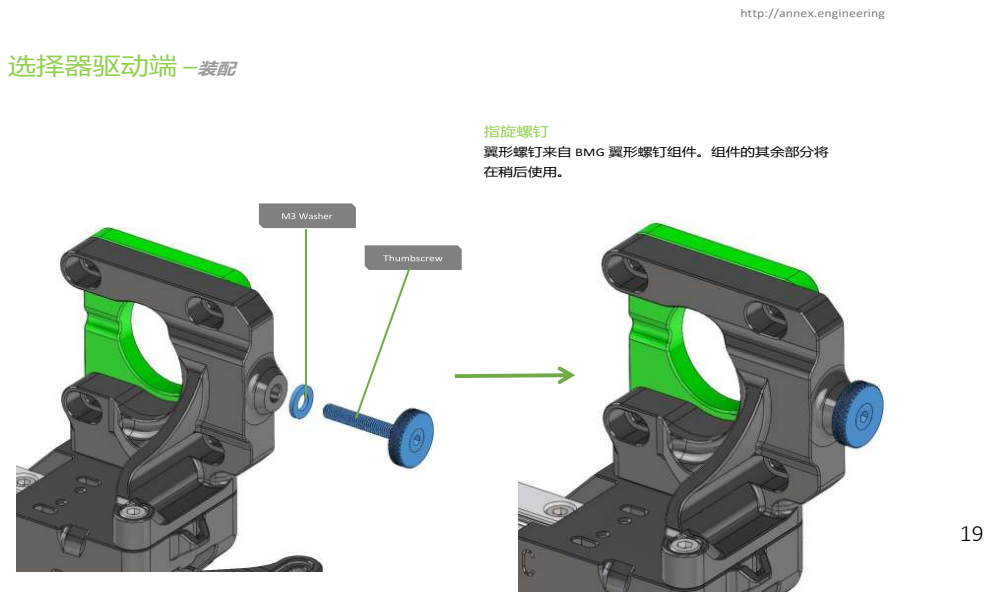
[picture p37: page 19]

指旋螺钉
翼形螺钉来自 BMG 翼形螺钉组件。组件的其余部分将
在稍后使用。

# 选择器驱动端 –装配

# 选择器驱动端 –装配

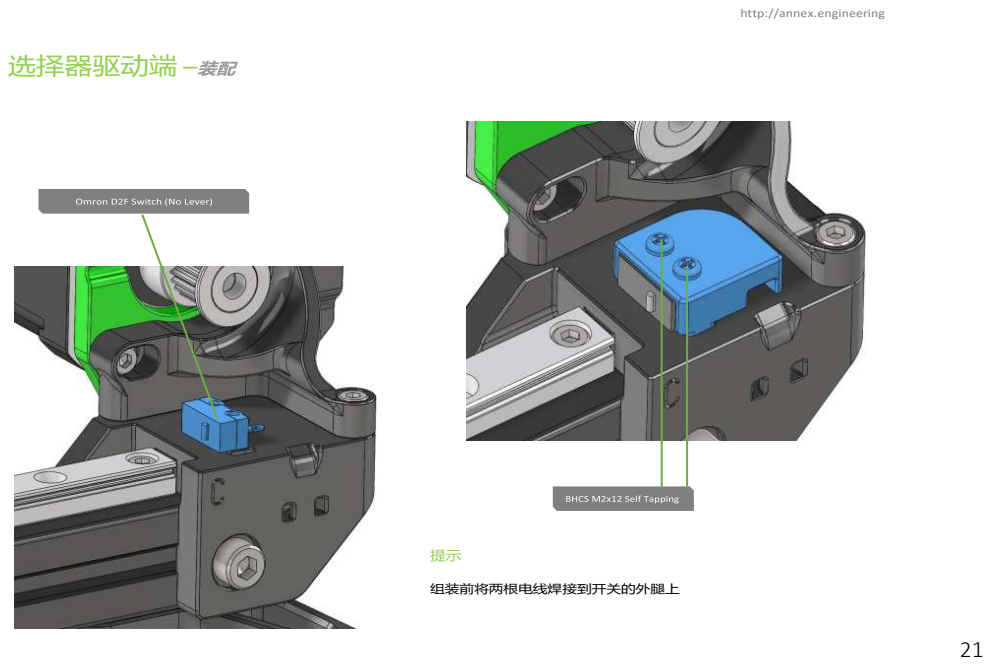
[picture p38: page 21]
组装前将两根电线焊接到开关的外腿上

此页有意留为空白

22

# 选择器模块 –概述

23

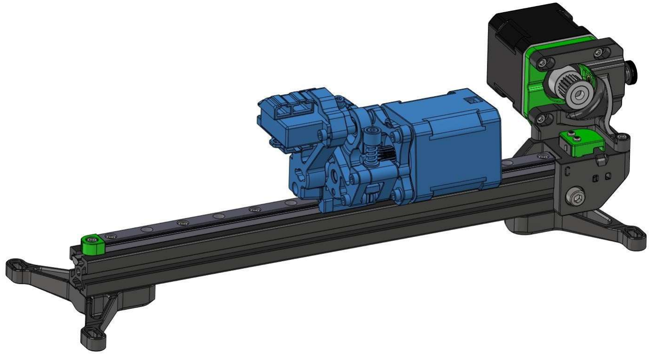
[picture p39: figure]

# 选择器模块 –装配

# 选择器模块 –装配

# 选择器模块 –装配

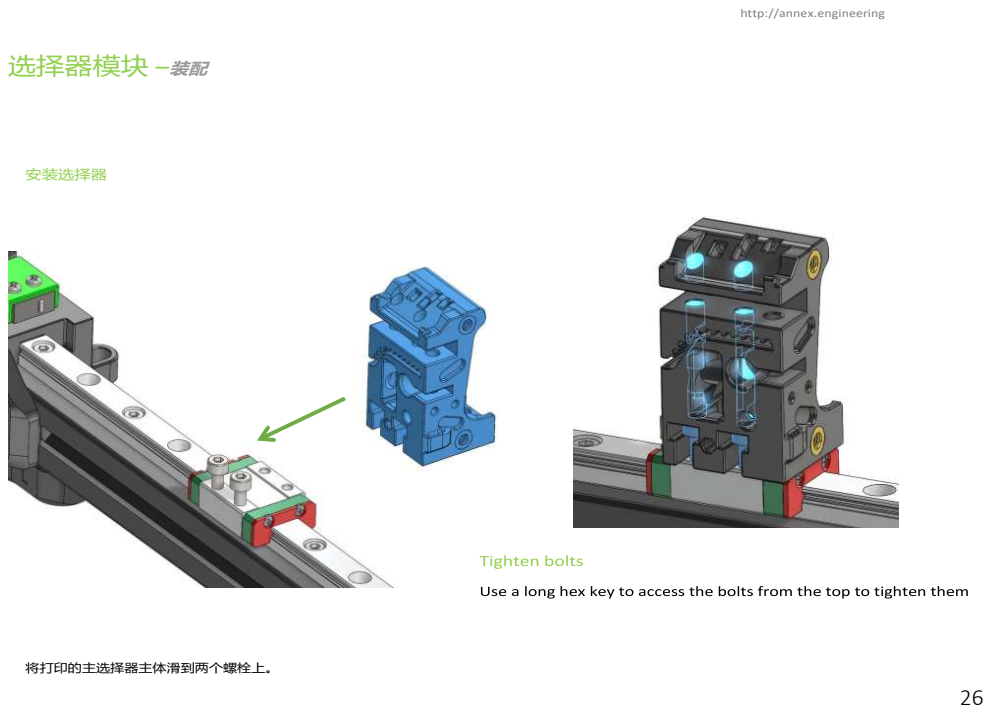
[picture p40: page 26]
安装选择器; 将打印的主选择器主体滑到两个螺栓上。

# 选择器模块 –装配

# 选择器模块 –装配

# 选择器模块 –装配

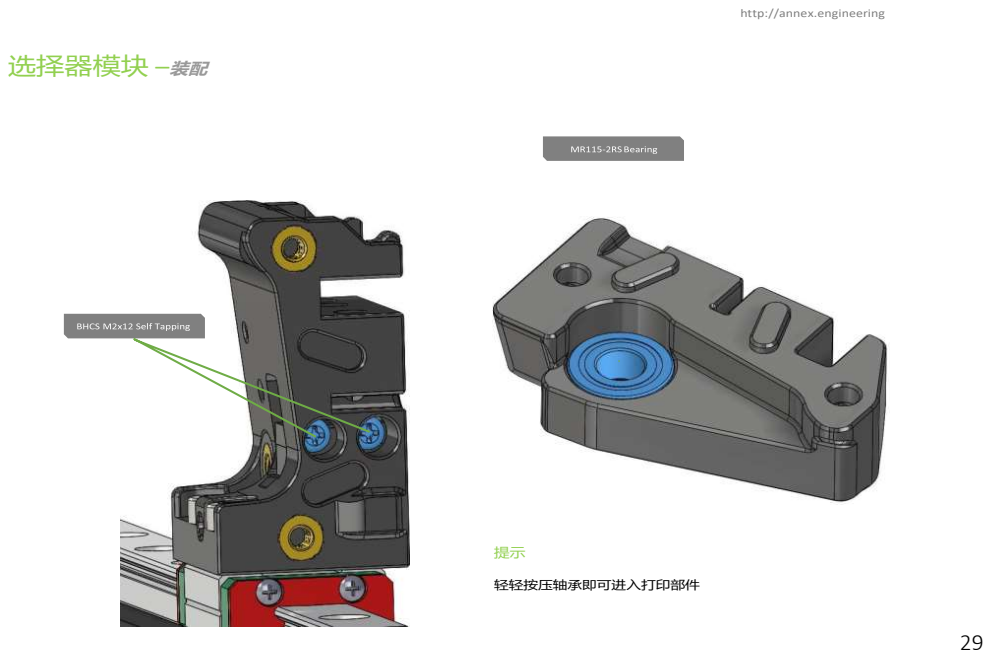
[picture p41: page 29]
轻轻按压轴承即可进入打印部件

# 选择器模块 –装配

# 选择器模块 –装配

SHCS M3x10（应用VC3）带垫圈

5x40mm 轴

印刷隔板

6毫米

轴

将 轴暴露在打印部件后部约6mm处 _ _

NEMA17（“灯丝驱动电机”）
31

# 选择器模块 –装配

# 选择器模块 –装配

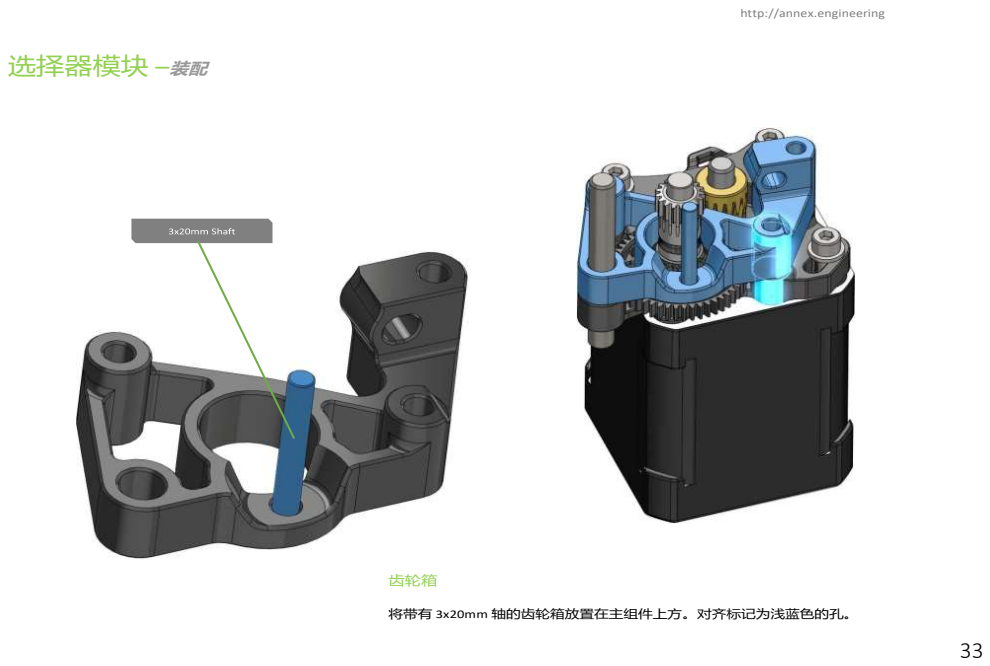
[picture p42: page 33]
齿轮箱

将带有 3x20mm 轴的齿轮箱放置在主组件上方。对齐标记为浅蓝色的孔。

# 选择器模块 –装配

# 选择器模块 –装配

# 选择器模块 –装配

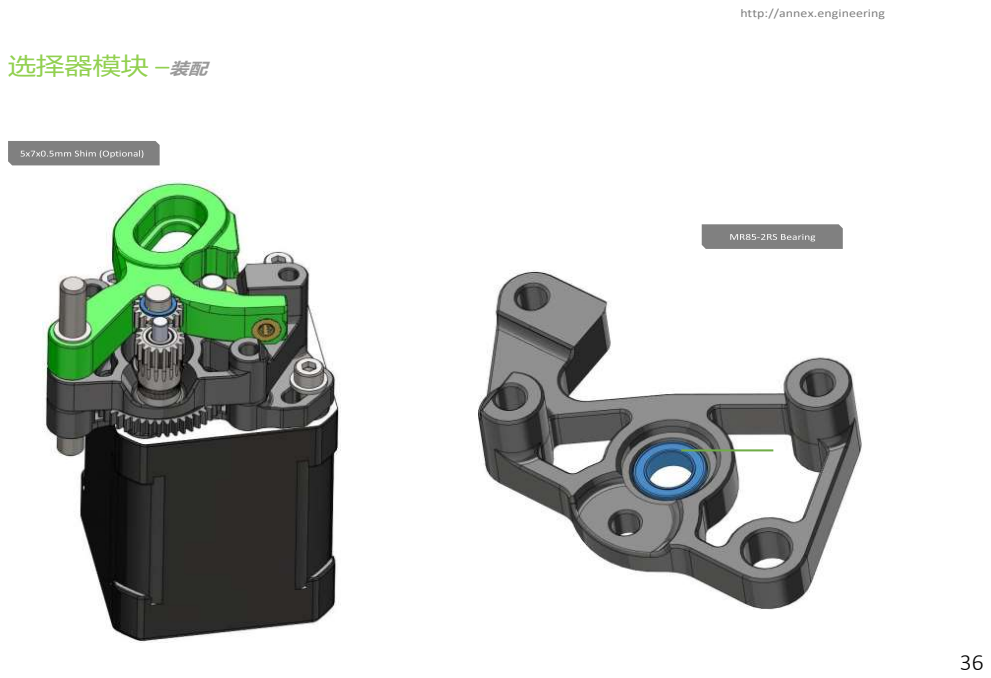
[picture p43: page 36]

# 选择器模块 –装配

# 选择器模块 –装配

弹簧和塑料垫圈来自 BMG 翼形螺钉组件。但是，请确保使用
M3x30 螺钉和印刷轴环而不是

# 选择器模块 –装配

### 操作说明

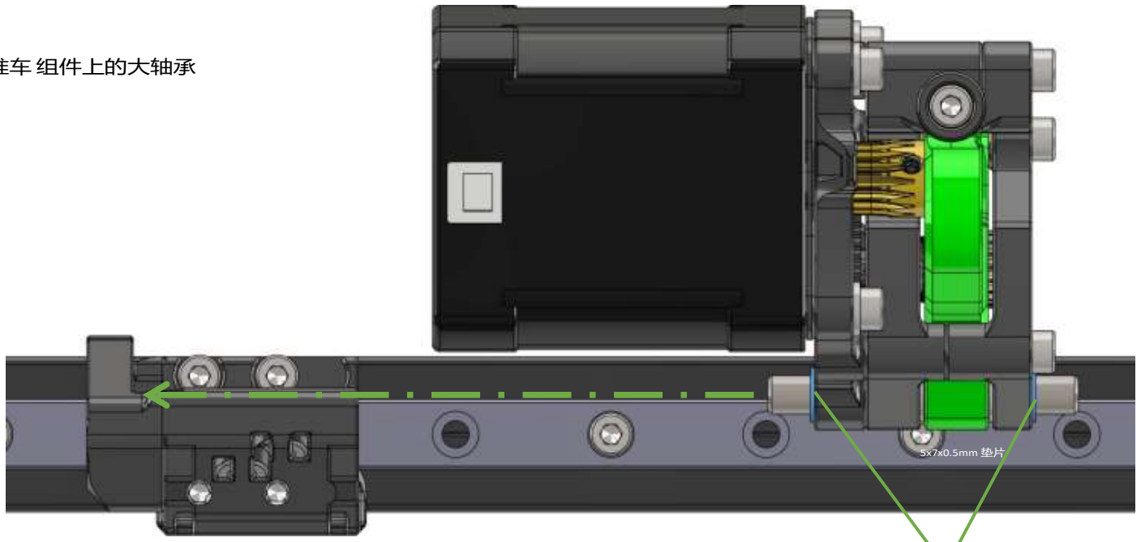
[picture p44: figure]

将 轴从选择器组件滑入推车 组件上的大轴承

39

# 选择器模块 –装配

MR115-2RS轴承

M3x5x4 插入件

M3x5x4 插入件

40

# 选择器模块 –装配

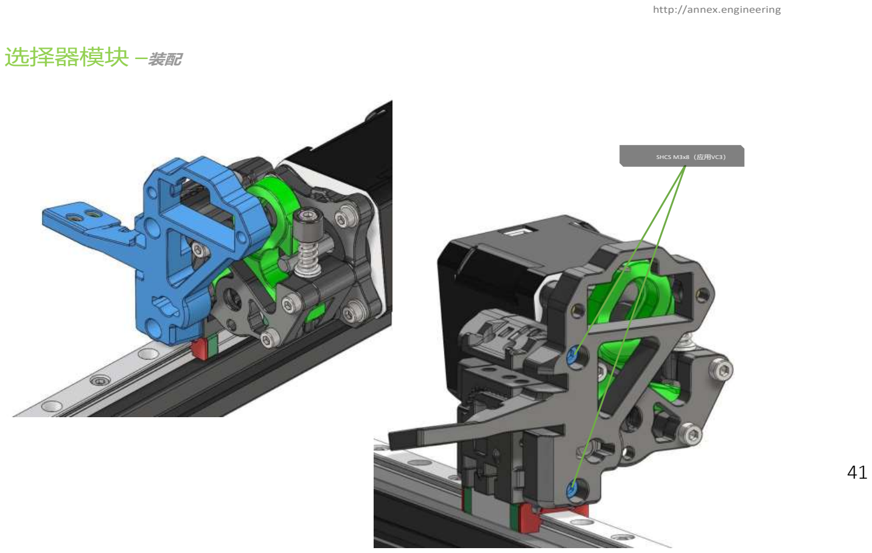
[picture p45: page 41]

SHCS M3x8（应用VC3）

41

# 选择器模块 –装配

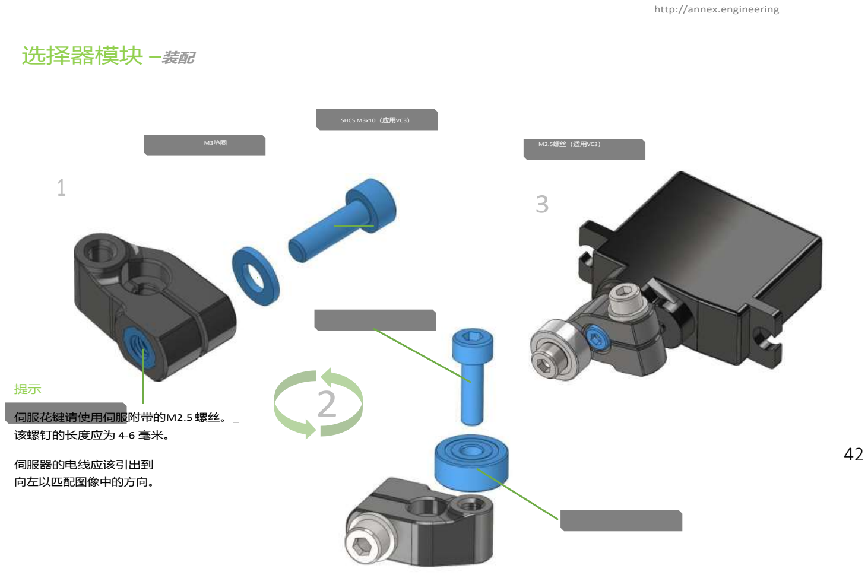
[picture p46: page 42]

SHCS M3x10（应用VC3）

M3垫圈
1

M2.5螺丝（适用VC3）

3

SHCS M3x10

M3x5x4 插入件

提示

伺服花键请使用伺服附带的M2.5螺丝。_
该螺钉的长度应为 4-6 毫米。

伺服器的电线应该引出到
向左以匹配图像中的方向。

623-2RS轴承
42

2

# 选择器模块 –装配

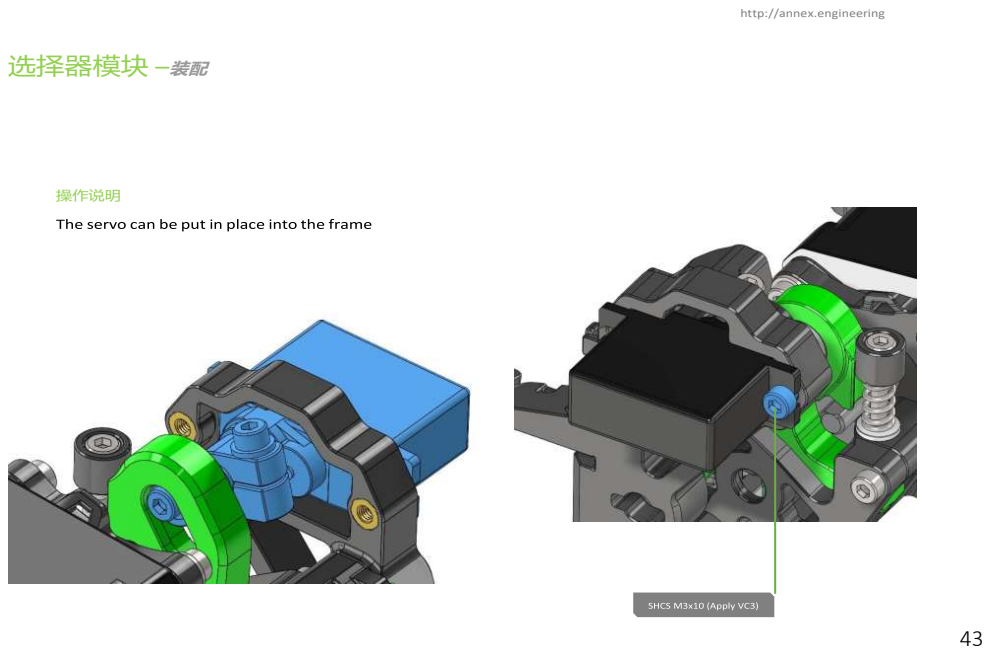
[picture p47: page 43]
操作说明

# 选择器模块 –装配

SHCS M3x16（应用VC3）

44

此页有意留为空白

45

# 灯丝通道模块 – 概述

46

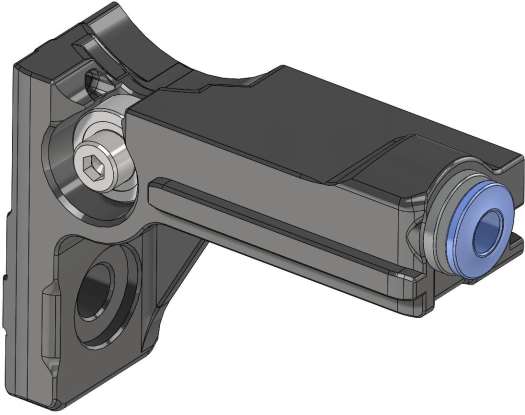
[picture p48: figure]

# 灯丝通道模块 –装配

# 灯丝通道模块 –装配

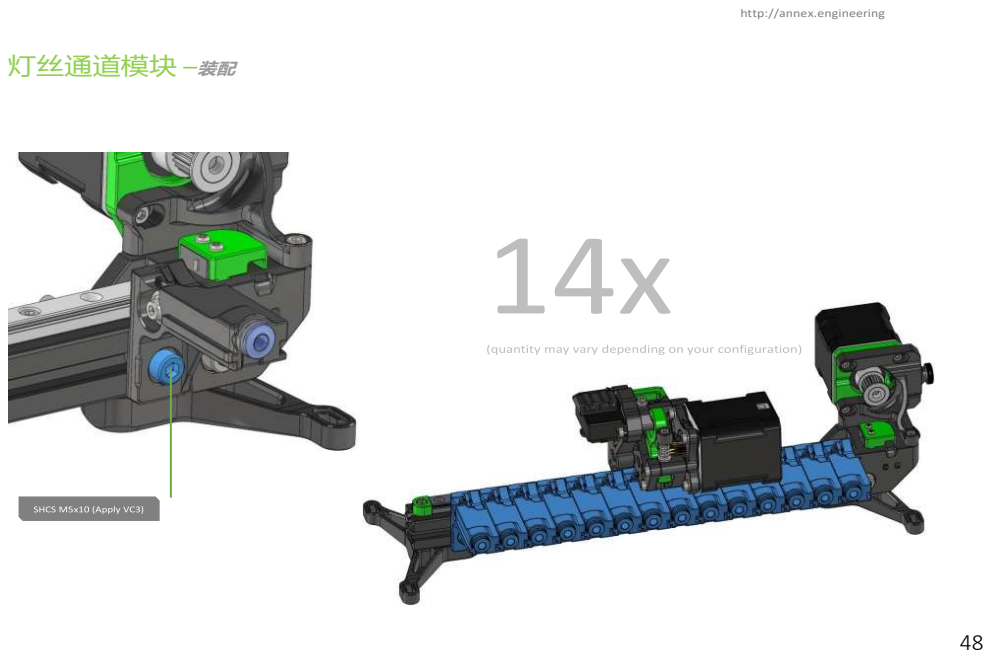
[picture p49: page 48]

# 灯丝通道模块 –装配

此页有意留为空白

50

# 选择惰轮端- 概述

51

# 选择器惰轮端部 – 装配

# 选择器惰轮端部 – 装配

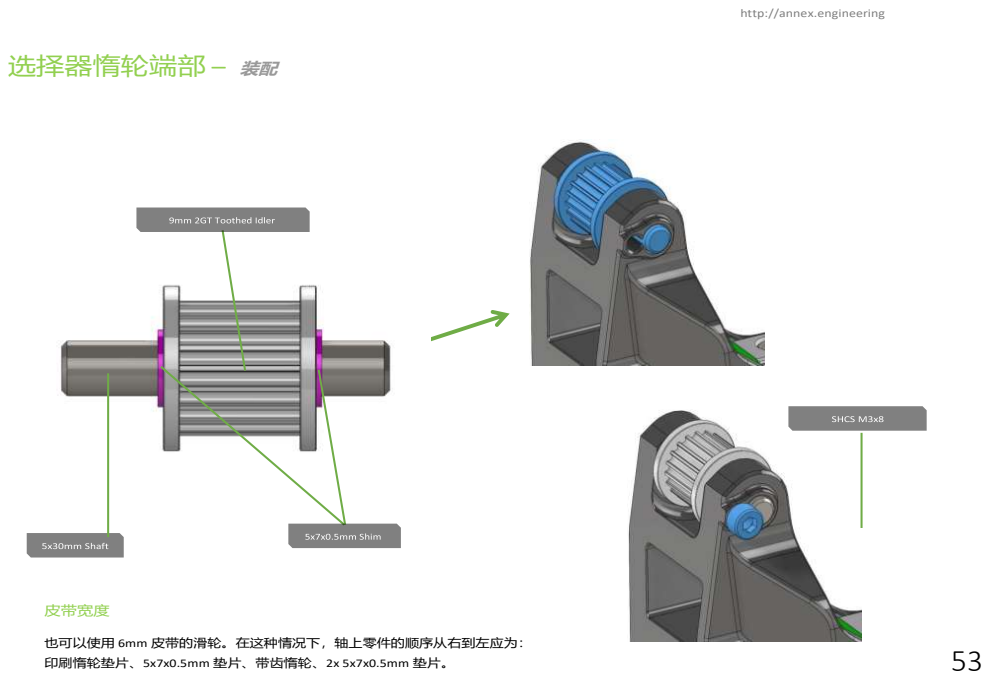
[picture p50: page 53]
皮带宽度; 印刷惰轮垫片、5x7x0.5mm 垫片、带齿惰轮、2x 5x7x0.5mm 垫片。

也可以使用 6mm 皮带的滑轮。在这种情况下，轴上零件的顺序从右到左应为：

# 传送带 –装配

1

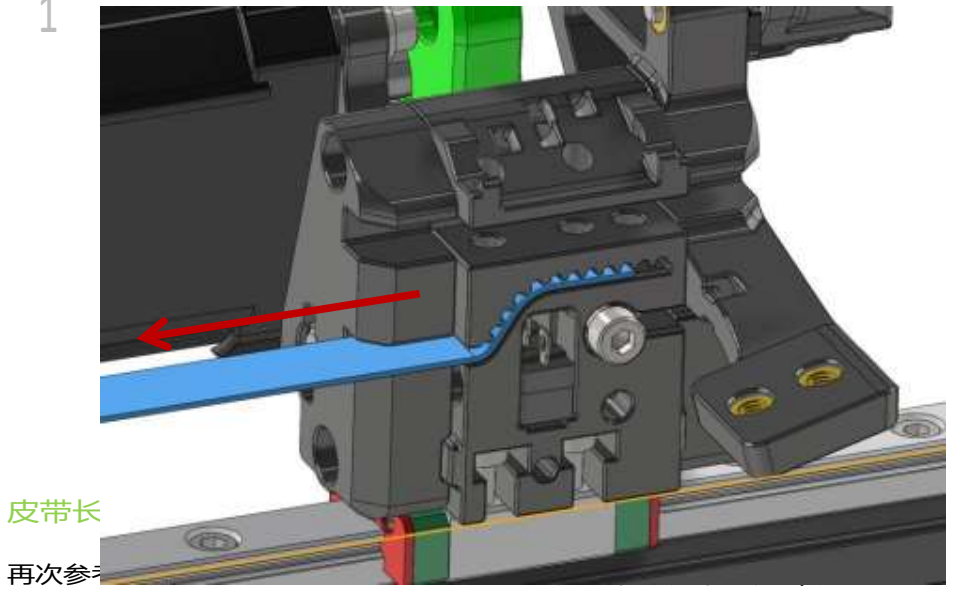
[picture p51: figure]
再次参考计算器，找到适合您的 Trad Rack 长度的推荐皮带长度（或
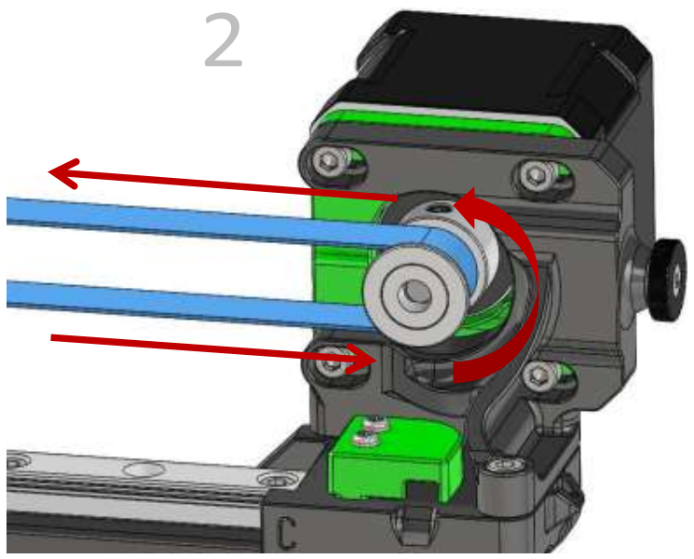
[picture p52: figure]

### 皮带长度

在运行后将皮带切割至所需长度）

54

# 传送带 –装配

3

4

55

# 传送带 –装配

通过将皮带折叠在 M3 螺栓上来固定皮带。如有必要，
修剪皮带末端以确保其不会突出右侧 托架的外表面。

# 传送带 –张紧

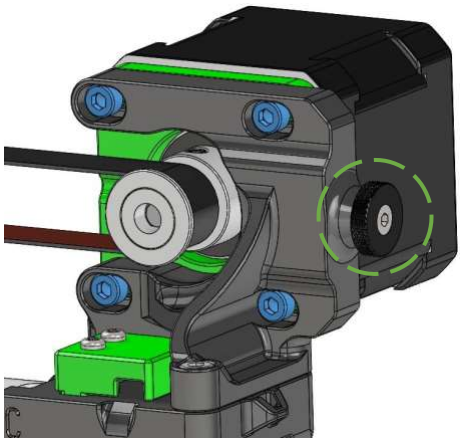
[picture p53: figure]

张紧

为了达到所需的皮带张力，松开固定步进电机的螺栓并
使用翼形螺钉进行调整。达到所需的张力后，再次拧紧
固定步进电机的所有螺栓。

57

# 电缆盖– 组装

此页有意留为空白

59

# 电缆链 – 概述

60

# 电缆链 – 装配

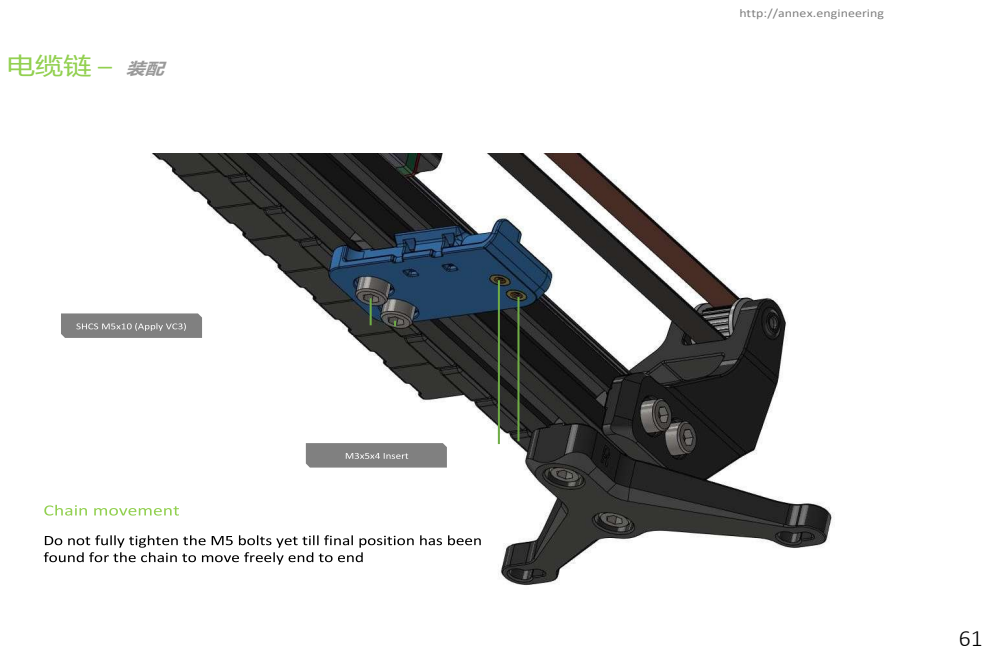
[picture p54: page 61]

# 电缆链 – 装配

安装前如有必要，翻转链条末端。使用底部的刚性端。

此页有意留为空白

63

## 控制器 –概述

64

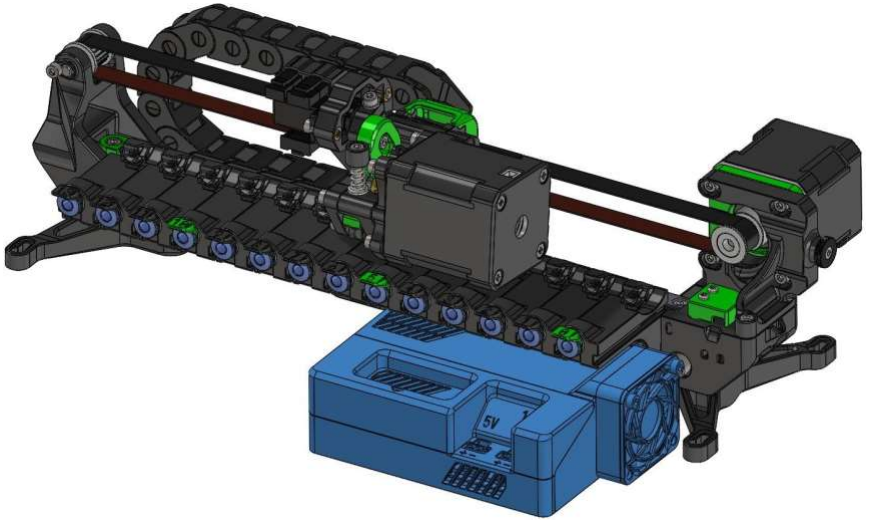
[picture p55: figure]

# 很快TM

# 星座: 星云

65

# 制作人员

感谢 您通过Annex Engineering建造Trad Rack 。 _ 我们谨向为本产品的开发和创造做出贡献的个人表示诚挚的谢意。虽然我们无法按特定顺序列出他们，但他们的努力对于使

Trad Rack焕然一新是非常宝贵的。

阿隆索240

Altvnk 安林

宝儿C1Rob

Cbon Churls

咖啡

Dalegaard

### 费米子

Lastone

Flukz 追

踪

Kmobs

iKirin

### 柯比·卢克

### 斯实验室

马特贝克心理

### 纽特托

### 帕佩杰利都灵

### 费米克奖

### 拉兹格里兹

可出租的袜子

Rincewind Ryan G

StrikeEagleCC Xile

### 亚奥维

我们对整个附件工程团队在整个开发过程中的奉献和辛勤工作 表示 感谢。_ 他们的专业知识和奉献精神对于 Trad Rack 的成功创建发挥了至关重要的作用。我们还要感谢 社区的持续支持和宝贵反馈。您的意见有助于帮助我们改进和完善Trad Rack 以满足您的需求和期望。

最后， 我们要感谢所有为本 手册做出贡献的人。 _ _ _ 您的努力确保了它为我们的用户提供全面、准确的信息，使他们能够充分利用Trad Rack 。

真挚地，

附楼工程团队

66

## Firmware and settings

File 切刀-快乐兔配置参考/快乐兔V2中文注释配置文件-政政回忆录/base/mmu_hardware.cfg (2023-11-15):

## Happy Hare MMU hardware config file with config for unknown
##
## Common external mcus:
## 1) EASY-BRD
##  J6 Jumper setting
##   Option 1: Pins 2-3 and 4-5, i.e.  .[..][..] (recommended)
##   This allows for option of "touch" selector setup. Note that this enables the option disables the "extra"
##   switch so the toolhead sensor (if used) would have to be connected to the main mcu
##
## Happy Hare MMU硬件配置文件
##
## 常见的外部MCU（微控制器）：
## 1）EASY-BRD
##  J6跳线设置
##   选项1：引脚2-3和4-5，即[..][..]（建议）
##   这允许选择“触摸”设置。请注意，这将启用该选项并禁用“额外”开关，因此工具头传感器（如果使用）必须连接到主MCU。
##
##   选项2：引脚1-2和4-5，即[..].[..]
##   如果您不关心选择器的触摸操作。 "额外"开关用于其他用途。
##
##  请注意，EASY-BRD不公开齿轮步进电机的DIAG引脚。
##
## 2）Fysetc Burrows ERB
##  Fysetc Burrows ERB板不需要跳线配置。选择器和齿轮的DIAG引脚都可用。
##
##  ERB固件刷写注意事项：
##   必须使用12V/24V电源供电
##    > make menuconfig（rpi2040，无引导程序）
##    > make
##  将卡片置于引导程序模式：按住'BOOTSEL'；点击'RST'；释放'BOOTSEL'
##    > make flash FLASH_DEVICE=2e8a:0003
##
## ------
##
## 关于“触摸”终点开关的说明：Happy Hare提供非常灵活的归位选项，可用于单个步进电机或同步步进电机。
## "触摸"选项利用了stallguard，并需要在TMC驱动程序部分设置适当的'diag_pin'和stallguard参数。如果已经公开了DIAG引脚，定义它们是无害的，因为只有在需要时才会使用和配置它们。
##
## 每个步进电机的“触摸”选项提供以下好处/可能性：
##  - 允许自动检测挤出步进电机的喷嘴位置！
##  - 允许自动检测选择器步进电机门口的卡塞和随后的恢复
##  - 允许自动检测齿轮步进电机的喂料口卡塞
##
## 这听起来很棒，对吧？的确如此，但有一些考虑因素：
##  - 外部EASY-BRD和ERB MCU在检测stallguard时性能不佳，经常导致“低电压错误”。通常情况下，可以调整选择器的触摸（TMC2209），特别是如果将'stealthchop_threshold'设置为大于归位速度且小于行程速度的值。也就是说，在归位过程中，步进电机以stealthchop模式运行。 [klipper专家会知道，在自动切换芯片模式为stealthchop，然后在归位后自动切换回spreadcycle以支持Stallguard2；但是，自动切换回spreadcycle会触发错误条件。正确设置'stealthchop_threshold'可以避免这种情况。我确定我说的比你想知道的要多！
##  - 在EASY-BRD和ERB MCU上启用齿轮步进电机的触摸不是一个明智的选择，因为您确实需要来自spreadcycle的额外扭矩，因此调整'stealthchop_threshold'并不是一个真正的选择。
##  - 对于挤出步进电机启用触摸是可行的，但您可能需要更改主MCU上的跳线以公开挤出步进电机驱动程序的DIAG引脚。
##
## 总之，“触摸”归位是您的MMU的高级选项，需要耐心和谨慎的调整。幸运的是，一切都可以使用常规终点开关正常工作，并且对于一些归位点的缺失，有创造性的解决方案。我对您想出的创意设置非常感兴趣。随时在Discord上联系我（moggieuk#6538）。
##
## 有关串行定义和引脚别名，请参考mmu.cfg
## 请随时提出任何进一步的
[mmu_config_setup]			                        # 用于自动获取挤出机配置的神奇助手

# 可归位挤出机 --------------------------------------------------------------------------------------------------
# 对于Happy Hare，将挤出机步进电机定义移动到这里非常重要，以便允许复杂的归位和同步选项。
# 这个定义将替换你现有的 [extruder] 定义中的步进电机定义部分。

# 重要提示：将与常规 [extruder] 相关的完整步进电机驱动器配置移动到这里，并注释掉
# printer.cfg 中原始的驱动器配置。
[tmc2209 manual_extruder_stepper extruder]
uart_pin: sb2040:gpio8                              # uart通讯端口Pin脚定义
# uart_address: 1                                     # 在 ERB 主板上取消注释
interpolate: false                                  # 是否开启256微步插值
run_current: 0.55			                        # LDO 36STH20-1004AHG。与下面的宏匹配
hold_current: 0.2                                   # 电机保持运行电流值
sense_resistor: 0.110                               # 驱动采样电阻值（不要修改）默认是0.110欧姆
stealthchop_threshold: 0		                    # 静音阀值 0：Spreadcycle模式（适用于挤出机）

# 如果你使用TMC并希望能够使用无限位归零到喷嘴，请取消下面两行的注释
#diag_pin: E_DIAG			# 设置为连接到TMC DIAG引脚的MCU引脚，用于挤出机
#driver_SGTHRS: 100			# 255是最敏感的值，0是最不敏感的


# 注意：在文件中稍早的 [mmu_config_setup] 行将自动获取所需的 [extruder] 步进电机配置
# 选项，因此你现在只需要添加补充选项，如终点开关！
# 但是，如果你决定在这里定义打印机的挤出机步进电机，则有效的配置选项仅限于：
#    step_pin, dir_pin, enable_pin, rotation_distance, gear_ratio, 
#    microsteps, full_steps_per_rotation
#    pressure_advance, pressure_advance_smooth_time
# 其他选项请保留在 [extruder] 配置中
[manual_extruder_stepper extruder]
step_pin: sb2040:gpio9                              # 电机脉冲引脚设置
dir_pin: !sb2040:gpio10                             # 电机方向引脚设置，可以通过添或删除引脚前面的!来改变电机的运转方向
enable_pin: !sb2040:gpio7                           # 电机使能引脚设置，引脚在pin之前应带有“!”
gear_ratio: 50:10							        # 齿轮比（BMG为50:17，SB为50：10输出轴：输入轴） 
microsteps: 64 				                        # 推荐设置 8或者16. 避免 'Timer too close' error 
full_steps_per_rotation: 200		                # 电机单圈所需脉冲数（1.8度电机:200，0.9度电机:400）

##  挤出长度校准
##	如果你想挤出100mm的料，但实际挤出了98mm
##	rotation_distance = <下行旧_rotation_distance 值> * <实际挤出量> / <目标挤出量>
##	rotation_distance = 22.6789511 * 98 / 100
##  22.6789511 是个比较好的初始值，修改下行代码后去掉代码前的注释符
rotation_distance: 22.6556595                       # 挤出值
pressure_advance_smooth_time: 0.001                 # 压力提前平滑时间

# 取消下面两行的注释以启用将“触摸”归位选项应用于喷嘴！
#extra_endstop_pins: tmc2209_extruder:virtual_endstop
#extra_endstop_names: mmu_ext_touch


# 耗材齿轮步进电机  ---------------------------------------------------------------------------------------------
# 注意，如果定义了工具头传感器，将自动添加 'mmu toolhead' 终止开关
# 默认值经过测试适用于 BOM NEMA14 电机。请根据您使用的电机调整这些值
# 例如：对于 NEMA17 电机，通常会使用更高的电流
[tmc2209 manual_extruder_stepper gear_stepper]
uart_pin: mmu:gpio9                                 # uart通讯端口Pin脚定义
interpolate: true                                   # 是否开启256微步插值
run_current: 0.5			                        # NEMA14 电机
hold_current: 0.1                                   # 电机保持运行电流值
sense_resistor: 0.110                               # 驱动采样电阻值（不要修改）默认是0.110欧姆
stealthchop_threshold: 0		                    # 静音阀值 0：Spreadcycle模式（适用于挤出机）
# 如果您有 TMC 电机并希望使用齿轮电机进行 "touch" 归位，请取消注释下面的两行
# diag_pin: ^mmu:MMU_GEAR_DIAG                      # 设置为连接到齿轮电机 TMC DIAG 引脚的 MCU 引脚
# driver_SGTHRS: 60                                 # 255 是最敏感的值，0 是最不敏感的值

[manual_extruder_stepper gear_stepper]
step_pin: mmu:gpio7                                 # 电机脉冲引脚设置
dir_pin: !mmu:gpio8                                 # 电机方向引脚设置，可以通过添或删除引脚前面的!来改变电机的运转方向
enable_pin: !mmu:gpio6                              # 电机使能引脚设置，引脚在pin之前应带有“!”
gear_ratio: 50:17                                   # 齿轮比（BMG齿轮比为50：17，输出轴在前，输入轴在后）
microsteps: 16                                      # 推荐 8 或 16。尝试两者以避免 Klipper 的 'Timer too close' 错误（也尝试调整 num_moves）
full_steps_per_rotation: 200                        # 1.8 度电机为 200，0.9 度电机为 400
velocity: 100                                       # 最大回抽速度
accel: 400                                          # 最大回抽加速度

##  挤出长度校准
##	如果你想挤出100mm的料，但实际挤出了98mm
##	rotation_distance = <下行旧_rotation_distance 值> * <实际挤出量> / <目标挤出量>
##	rotation_distance = 22.6789511 * 98 / 100
##  22.6789511 是个比较好的初始值，修改下行代码后去掉代码前的注释符
rotation_distance: 22.213836                        # 挤出值

# 如果要启用齿轮电机进行 "touch" 归位选项，请取消注释下面的两行
# extra_endstop_pins: tmc2209_gear_stepper:virtual_endstop
# extra_endstop_names: mmu_gear_touch

# 选择器电机  --------------------------------------------------------------------------------------------------------
[tmc2209 manual_mh_stepper selector_stepper]
uart_pin: mmu:gpio0                                 # uart通讯端口Pin脚定义
# uart_address: 1                                     # 在 ERB 主板上取消注释
run_current: 0.4                                    # NEMA14 电机
hold_current: 0.2                                   # 如果不使用触摸归位或移动（TMC stallguard），可以设置得更小
interpolate: True                                   # 是否开启256微步插值
sense_resistor: 0.110                               # 驱动采样电阻值（不要修改）默认是0.110欧姆
stealthchop_threshold: 100                          # 使用 stealthchop 进行归位（较慢速度）效果最佳
# 如果您有 TMC 电机并希望使用选择器进行 "touch" 移动和归位，请取消注释下面的两行
# diag_pin: ^mmu:MMU_SEL_DIAG                       # 设置为连接到选择器电机 TMC DIAG 引脚的 MCU 引脚
# driver_SGTHRS: 75                                 # 255 是最敏感的值，0 是最不敏感的值

[manual_mh_stepper selector_stepper]
step_pin: mmu:gpio2                                 # 电机脉冲引脚设置
dir_pin: !mmu:gpio1                                 # 电机方向引脚设置，可以通过添或删除引脚前面的!来改变电机的运转方向
enable_pin: !mmu:gpio3                              # 电机使能引脚设置，引脚在pin之前应带有“!”
rotation_distance: 40                               # 主动带轮周长mm（2GT-20T带轮40，2GT-16T带轮32）
microsteps: 16                                      # 不需要高精度
full_steps_per_rotation: 200                        # 1.8 度电机为 200，0.9 度电机为 400
velocity: 200                                       # 最大速度
accel: 1200                                         # 最大加速度
endstop_pin: !mmu:gpio20                            # 选择器限位开关引脚
endstop_name: mmu_sel_home                          # 限位开关名称
# 如果要提供选择器 "touch" 移动和归位选项，请取消注释下面的两行
# extra_endstop_pins: tmc2209_selector_stepper:virtual_endstop
# extra_endstop_names: mmu_sel_touch

# 工具头传感器  ---------------------------------------------------------------------------------------------------------
# 取消注释此部分以启用工具头传感器支持。只需定义开关引脚；其他常规的
# filament_switch 选项与 MMU 操作不兼容，将干扰 MMU 操作。注意，这将自动
# 定义 "mmu_toolhead" 终止开关（归位点）以进行加载和卸载
## MMU Toolhead sensor START
[filament_switch_sensor toolhead_sensor]
switch_pin: sb2040:gpio29

# 舵机设置 -----------------------------------------------------------------------------------------------------------
# 基本舵机 PWM 设置。如果更改这些值，不同位置的角度定义也会更改
[mmu_servo mmu_servo]
pin: mmu:gpio21
maximum_servo_angle: 180
minimum_pulse_width: 0.001                          # 0.00085# 最小脉冲宽度时间（秒）默认值为0.001
maximum_pulse_width: 0.002                          # 0.00215# 最大脉冲宽度时间（秒）默认值为0.002
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

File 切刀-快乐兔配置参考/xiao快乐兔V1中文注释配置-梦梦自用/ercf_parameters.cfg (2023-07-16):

[ercf]

# Servo configuration  -----------------------------------------------------------------------------------------------------
servo_up_angle: 180	# Default: MG90S servo: Up=30    ; SAVOX SH0255MG: Up=140
servo_down_angle: 40	# Default: MG90S servo: Down=140 ; SAVOX SH0255MG: Down=30


# Gear stepper load/unload speeds ------------------------------------------------------------------------------------------
# Long moves are faster than the small ones and used for the bulk of the bowden movement
# 100mm/s should be "quiet" with the NEMA14 motor or a NEMA17 pancake, but you can go lower for really low noise
long_moves_speed:  70			# mm/s. Conservative value is 100mm/s, Max around 300mm/s
short_moves_speed: 40			# mm/s. Conservative value is 35mm/s. Max around 100mm/s


# Logging ------------------------------------------------------------------------------------------------------------------
# log_level & logfile_level can be set to one of (0 = essential, 1 = info, 2 = debug, 3 = trace, 4 = developer)
# Generally you can keep console logging to a minimal whilst still sending debug output to the ercf.log file
# Increasing the console log level is only really useful during initial setup to save having to constantly open the log file
# 记录 ---------------------------------------------- ---------------------------------------------- ------------------
# log_level & logfile_level 可以设置为 (0 = essential, 1 = info, 2 = debug, 3 = trace, 4 = developer)
# 通常，您可以将控制台日志记录保持在最低限度，同时仍将调试输出发送到 ercf.log 文件
# 增加控制台日志级别仅在初始设置期间真正有用，以节省不断打开日志文件的麻烦
log_level: 1
logfile_level: 3			# Can also be set to -1 to disable log file completely
log_statistics: 1 			# 1 to log statistics on every toolchange, 0 to disable (but still recorded)
log_visual: 1				# 1 log visual representation of filament, 2 shortened KlipperScreen friendly, 0 disable
startup_status: 0			# Whether to log tool to gate status on startup, 1 = summary, 2 = full, 0 = disable


# Bowden tube movement -----------------------------------------------------------------------------------------------------
# Base value for the loading length used by the auto-calibration macro. Please use a value SMALLER than the real reverse
# bowden length (by about 30-40mm). This is ONLY used during calibration, and has no impact on normal running after calibration
# 鲍登管运动-------------------------------------------- ---------------------------------------------- ------
# 自动校准宏使用的加载长度的基值。请使用比实际反转小的值
# 鲍登长度（约 30-40 毫米）。仅在校准时使用，校准后不影响正常运行
calibration_bowden_length: 750
#
# If you are getting "timer too close" errors, increase the number of moves used during long loading and unloading moves
# 如果你遇到“timer too close”错误，增加长时间加载和卸载移动中使用的移动次数
num_moves: 2				# Number of moves to make when loading or unloading bowden
#
# If enabled, the driver will "believe" the encoder reading and make correction moves to bring the filament to the desired
# end of bowden position. This is useful is you suspect slippage on high speed loading (but requires accurate encoder)
# If disabled, the gear stepper will be solely responsible for filament positioning in bowden (requires minimal friction)
# 如果启用，驱动程序将“相信”编码器读数并进行修正，使灯丝达到所需
# 鲍登位置结束。如果您怀疑高速加载时会打滑（但需要精确的编码器），这很有用
# 如果禁用，齿轮步进器将全权负责鲍登灯丝的定位（需要最小的摩擦力）
apply_bowden_correction: 1

# When using 'apply_bowden_correction' how close in mm the correction moves will attempt to get to target (unload mirrors this value)
# 使用“apply_bowden_correction”时，校正移动将尝试接近目标（卸载反映了此值）
load_bowden_tolerance: 10.0
# Filament homing, loading and unloading controls -------------------------------------------------------------------------
# If you have a toolhead sensor for filament homing:
# 耗材归位、装卸控制---------------------------------------- ------------------------------
# 如果您有用于灯丝归位的工具头传感器：
toolhead_homing_max: 20			# Maximum distance to advance in order to attempt to home to toolhead sensor (default 20)
toolhead_homing_step: 1		# Step size to use when homing to the toolhead sensor (default 1)
#
# Options without toolhead sensor (but still needed for calibration with toolhead sensor)
# 没有工具头传感器的选项（但仍然需要使用工具头传感器进行校准）
extruder_homing_max: 25			# Maximum distance to advance in order to attempt to home the extruder
extruder_homing_step: 2.0		# Step size to use when homing to the extruder with collision detection (default 2)
#
# For accurate homing and to avoid grinding, tune the gear stepper current reduction (currently TMC2209 only)
# To ensure no skipping during fast tip-forming moves, tune the extruder current increase (currently TMC2209 only)
#为了准确归位和避免磨削，调整齿轮步进电流减少（目前仅限TMC2209）
# 为确保在快速成型过程中不会发生跳跃，请调整挤出机电流增量（目前仅限 TMC2209）
extruder_homing_current: 40		# Percentage of gear_stepper current (20%-100%) to use when homing to extruder homing (100 to disable)
extruder_form_tip_current: 100		# Percentage of extruder current (100%-150%) to use when forming tip (100 to disable)
#
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

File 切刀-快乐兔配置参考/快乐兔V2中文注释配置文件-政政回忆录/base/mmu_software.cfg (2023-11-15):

## Happy Hare 支持宏

[save_variables]
filename: /home/klipper/printer_data/config/mmu/mmu_vars.cfg

########################################################################
# 刀具更换宏
# 这是在安装时自动生成的，但您可以增加或减少此列表以匹配您实际使用的刀具数量
#######################################################################
[gcode_macro T0]
gcode: MMU_CHANGE_TOOL TOOL=0
[gcode_macro T1]
gcode: MMU_CHANGE_TOOL TOOL=1
[gcode_macro T2]
gcode: MMU_CHANGE_TOOL TOOL=2
[gcode_macro T3]
gcode: MMU_CHANGE_TOOL TOOL=3
[gcode_macro T4]
gcode: MMU_CHANGE_TOOL TOOL=4
[gcode_macro T5]
gcode: MMU_CHANGE_TOOL TOOL=5
[gcode_macro T6]
gcode: MMU_CHANGE_TOOL TOOL=6
[gcode_macro T7]
gcode: MMU_CHANGE_TOOL TOOL=7
[gcode_macro T8]
gcode: MMU_CHANGE_TOOL TOOL=8


########################################################################
# 简化的命令子集，仅用于在 Mainsail/Fluidd UI 中可见
# 在自定义面板完成之前，这是自动完成的！
# __ 是一个技巧，因为它不会在UI中显示，但在这里定义宏的事实意味着Mainsail/Fluidd仍然能看到它们
########################################################################
[gcode_macro MMU__EJECT]
gcode: MMU_EJECT

[gcode_macro MMU__HOME]
gcode:
    {% set TOOL = params.TOOL|default(0)|int %}
    {% set FORCE_UNLOAD = params.FORCE_UNLOAD|default(0)|int %}
    MMU_HOME TOOL={TOOL} FORCE_UNLOAD={FORCE_UNLOAD}

[gcode_macro MMU__STATUS]
gcode: MMU_STATUS

[gcode_macro MMU__MOTORS_OFF]
gcode: MMU_MOTORS_OFF

[gcode_macro MMU__SERVO]
gcode:
    {% set POS = params.POS|default("up")|string %}
    MMU_SERVO POS={POS}

[gcode_macro MMU__SELECT_TOOL]
gcode:
    {% set TOOL = params.TOOL|default(0)|int %}
    MMU_SELECT TOOL={TOOL}

[gcode_macro MMU__SELECT_BYPASS]
gcode: MMU_SELECT_BYPASS

[gcode_macro MMU__LOAD_BYPASS]
gcode: MMU_LOAD_BYPASS

[gcode_macro MMU__RECOVER]
gcode: MMU_RECOVER

[gcode_macro MMU__PRELOAD]
gcode:
    {% set GATE = params.GATE|default(0)|int %}
    MMU_PRELOAD GATE={GATE}

[gcode_macro MMU__CHECK_GATES]
gcode:
    {% set GATE = params.GATE|default(0)|int %}
    MMU_CHECK_GATES GATE={GATE}

# 有用的便利命令...

[gcode_macro MMU_CHANGE_TOOL_STANDALONE]
description: 用于在打印开始时加载初始刀具的便利宏（在 mmu_software.cfg 中定义）
gcode:
    {% set TOOL = params.TOOL|default(0)|int %}
    MMU_CHANGE_TOOL TOOL={TOOL} STANDALONE=1


########################################################################
# 单独调整喷嘴尖端形状（也有助于快速调整切片参数值）
########################################################################
[gcode_macro _MMU_FORM_TIP_STANDALONE]
description: 模拟SuperSlicer进程的独立宏

# 卸载和插料数值 - 形成和塑造尖端的初始移动
variable_unloading_speed_start: 80     # 快速移动，以将熔融区的塑料与丝材分离（非常初始的回退，SS使用距离为E-15）
variable_unloading_speed: 20           # 过快会形成过长的尖端或头发。在这里更慢更好 UNLOADING_SPEED_START/COOLING_MOVES 似乎是一个不错的起点
variable_ramming_volume: 0             # （mm^3）SS默认值 = 2, 5, 9, 13, 18, 23, 27。仅用于模拟独立的SS插料
variable_ss_ramming: 0                 # 设置为0以进行独立的插料（RAMMING_VOLUME），设置为1以让切片软件执行插料（即在独立模式下关闭）

# 冷却移动数值 - 用于冷却形成的尖端并将其与丝材分离
variable_cooling_tube_position: 35     # 从加热器块顶部到散热器顶部的距离 Dragon ST：35，Dragon HF：30，Mosquito：30，Revo：35，Phaetus Rapido HF：43；
variable_cooling_tube_length: 10       # 从喷嘴到加热器块顶部的距离 Dragon ST：15，Dragon HF：10，Mosquito：20，Revo：10，Phaetus Rapido HF：22；
variable_initial_cooling_speed: 10     # 缓慢以使尖端固化并冷却形成的丝材
variable_final_cooling_speed: 50       # 高速将分离的丝材拉断。过快会导致尖端变形。过慢会导致丝材拉得过长/无法分离
variable_toolchange_temp: 0            # 用于工具更换时降低温度，默认为0
variable_cooling_moves: 4              # 冷却移动次数 2-4 是一个不错的起点

# SkinnyDip数值 - 仅用于燃烧非常细小的毛发（不适用于长尖端重塑）
variable_use_skinnydip: 1              # 最后调整此值，仅用于去除非常细小的毛发（与长尖端不同）
variable_skinnydip_distance: 30        # 从Cooling_tube_position下方开始，根据插料量的使用情况逐渐增加
variable_dip_insertion_speed: 30       # 中慢速 - 恰好足够融化细小的毛发。过慢会拉断熔融的丝材
variable_dip_extraction_speed: 70      # 大约是插入速度的两倍，防止形成新的毛发
variable_melt_zone_pause: 0            # 毫秒 - 默认为0
variable_cooling_zone_pause: 0         # 毫秒 - 默认为0 - 如果需要在这里进行调整，可能是插入速度太慢了
variable_use_fast_skinnydip: 0         # 跳过SkinnyDip移动时的工具头温度更改 - 默认为0

# 最终排出 - 仅用于独立调整。由`MMU_FORM_TIP`命令自动设置
variable_final_eject: 0                # 默认为0，在独立调整过程中启用以排出丝材

# 将丝材停放准备排出
variable_parking_distance: 0           # 最终冷却移动后的丝材停放位置，0将保留丝材在其自然停留的位置

gcode:
    # 初始化参数
    {% set UNLOADING_SPEED_START = params.UNLOADING_SPEED_START|default(printer['gcode_macro _MMU_FORM_TIP_STANDALONE']['unloading_speed_start']) %}
    {% set UNLOADING_SPEED = params.UNLOADING_SPEED|default(printer['gcode_macro _MMU_FORM_TIP_STANDALONE']['unloading_speed']) %}
    {% set RAMMING_VOLUME = params.RAMMING_VOLUME|default(printer['gcode_macro _MMU_FORM_TIP_STANDALONE']['ramming_volume']) %}
    {% set SS_RAMMING = params.SS_RAMMING|default(printer['gcode_macro _MMU_FORM_TIP_STANDALONE']['ss_ramming']) %}
    {% set COOLING_TUBE_LENGTH = params.COOLING_TUBE_LENGTH|default(printer['gcode_macro _MMU_FORM_TIP_STANDALONE']['cooling_tube_length']) %}
    {% set COOLING_TUBE_POSITION = params.COOLING_TUBE_POSITION|default(printer['gcode_macro _MMU_FORM_TIP_STANDALONE']['cooling_tube_position']) %}
    {% set INITIAL_COOLING_SPEED = params.INITIAL_COOLING_SPEED|default(printer['gcode_macro _MMU_FORM_TIP_STANDALONE']['initial_cooling_speed']) %}
    {% set FINAL_COOLING_SPEED = params.FINAL_COOLING_SPEED|default(printer['gcode_macro _MMU_FORM_TIP_STANDALONE']['final_cooling_speed']) %}
    {% set COOLING_MOVES = params.COOLING_MOVES|default(printer['gcode_macro _MMU_FORM_TIP_STANDALONE']['cooling_moves']) %}
    {% set TOOLCHANGE_TEMP = params.TOOLCHANGE_TEMP|default(printer['gcode_macro _MMU_FORM_TIP_STANDALONE']['toolchange_temp']) %}
    {% set USE_SKINNYDIP = params.USE_SKINNYDIP|default(printer['gcode_macro _MMU_FORM_TIP_STANDALONE']['use_skinnydip']) %}
    {% set USE_FAST_SKINNYDIP = params.USE_FAST_SKINNYDIP|default(printer['gcode_macro _MMU_FORM_TIP_STANDALONE']['use_fast_skinnydip']) %}
    {% set SKINNYDIP_DISTANCE = params.SKINNYDIP_DISTANCE|default(printer['gcode_macro _MMU_FORM_TIP_STANDALONE']['skinnydip_distance']) %}
    {% set DIP_INSERTION_SPEED = params.DIP_INSERTION_SPEED|default(printer['gcode_macro _MMU_FORM_TIP_STANDALONE']['dip_insertion_speed']) %}
    {% set DIP_EXTRACTION_SPEED = params.DIP_EXTRACTION_SPEED|default(printer['gcode_macro _MMU_FORM_TIP_STANDALONE']['dip_extraction_speed']) %}
    {% set MELT_ZONE_PAUSE = params.MELT_ZONE_PAUSE|default(printer['gcode_macro _MMU_FORM_TIP_STANDALONE']['melt_zone_pause']) %}
    {% set COOLING_ZONE_PAUSE = params.COOLING_ZONE_PAUSE|default(printer['gcode_macro _MMU_FORM_TIP_STANDALONE']['cooling_zone_pause']) %}
    {% set PARKING_DISTANCE = params.PARKING_DISTANCE|default(printer['gcode_macro _MMU_FORM_TIP_STANDALONE']['parking_distance']) %}
    {% set FINAL_EJECT = params.FINAL_EJECT|default(printer['gcode_macro _MMU_FORM_TIP_STANDALONE']['final_eject']) %}

    G91
    M83
    G92 E0
    
    #---------------------------------#
    #-喷嘴成型过程从这里开始-#
    #---------------------------------#

    SET_PRESSURE_ADVANCE ADVANCE=0
    {% set OLD_TEMP = printer.extruder.target %}
    {% if SS_RAMMING|int == 0 and RAMMING_VOLUME|int > 0 %} # Standalone Ramming
        {% set RATIO = (RAMMING_VOLUME|float) /23.0 %}
        G1 E{0.5784 * RATIO|float} F299 #7
        G1 E{0.5834 * RATIO|float} F302 #3
        G1 E{0.5918 * RATIO|float} F306 #6
        G1 E{0.6169 * RATIO|float} F319 #6
        G1 E{0.3393 * RATIO|float} F350 #0
        G1 E{0.3363 * RATIO|float} F350 #0
        G1 E{0.7577 * RATIO|float} F392 #6
        G1 E{0.8382 * RATIO|float} F434 #3
        G1 E{0.7776 * RATIO|float} F469 #9
        G1 E{0.1293 * RATIO|float} F469 #9
        G1 E{0.9673 * RATIO|float} F501 #2
        G1 E{1.0176 * RATIO|float} F527 #2
        G1 E{0.5956 * RATIO|float} F544 #6
        G1 E{0.4555 * RATIO|float} F544 #6
        G1 E{1.0662 * RATIO|float} F552 #4
    {% endif %}

    # 在从熔融区域提取挤出物之前，设置工具温度，并等待设定点
    # （SKINNYDIP - 仅适用于正常模式）
    # 仅在更换不同类型的挤出物时使用，例如 ABS-->PLA
    {% if TOOLCHANGE_TEMP|float > 0 and USE_FAST_SKINNYDIP|int == 0 %}
         M109 S{TOOLCHANGE_TEMP}
    {% endif %}

    # 卸载 - 这是喷嘴尖部形状的来源，速度更快=细长/尖细/更高的线头
    {% set TOTAL_RETRACTION_DISTANCE = COOLING_TUBE_POSITION|float + COOLING_TUBE_LENGTH|float / 2 - 15 %}
    G1 E-15 F{1.0 * UNLOADING_SPEED_START|float * 60} # Default value from SS - Cannot modify
    G1 E-{0.7 * TOTAL_RETRACTION_DISTANCE} F{1.0 * UNLOADING_SPEED|float * 60}
    G1 E-{0.2 * TOTAL_RETRACTION_DISTANCE} F{0.5 * UNLOADING_SPEED|float * 60}
    G1 E-{0.1 * TOTAL_RETRACTION_DISTANCE} F{0.3 * UNLOADING_SPEED|float * 60}

    {% if TOOLCHANGE_TEMP|float > 0 and USE_FAST_SKINNYDIP|int == 1 %}
        M104 S{TOOLCHANGE_TEMP}
    {% endif %}

    # 生成冷却移动 - 固化喷嘴尖形状，并帮助打断形成的线头
    {% set SPEED_INC = (FINAL_COOLING_SPEED|float - INITIAL_COOLING_SPEED|float) / (2 * COOLING_MOVES|float - 1) %}
    {% for move in range(COOLING_MOVES|int) %}
        G1 E{COOLING_TUBE_LENGTH} F{(INITIAL_COOLING_SPEED|float + SPEED_INC*move*2) * 60}
        G1 E-{COOLING_TUBE_LENGTH} F{(INITIAL_COOLING_SPEED|float + SPEED_INC*(move*2+1)) * 60}
    {% endfor %}
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

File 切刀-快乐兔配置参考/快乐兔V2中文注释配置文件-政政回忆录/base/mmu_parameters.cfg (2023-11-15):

[mmu]
# 厂商和版本配置对于定义MMU的功能非常重要
# ERCF
# 1.1 原始设计，为Sprigy添加"s"后缀，为Binky添加"b"后缀，为Triple-Decky添加"t"后缀
#     例如："1.1sb"表示v1.1与Springy模块和Binky编码器
# 2.0 新的社区版 ERCF
# Tradrack
#  - 即将推出
# Prusa
#  - 即将推出
mmu_vendor: ERCF						# MMU家族
mmu_version: 1.1						# MMU硬件版本号（添加上面文档中的后缀）
mmu_num_gates: 9 						# 选择器门的数量


# 舵机配置  -----------------------------------------------------------------------------------------------------
# 伺服的三个命名位置的角度：
#   up   = 选择工具并允许丝材自由通过门
#   down = 夹持丝材
#   move = 准备好伺服以进行选择器移动（可选 - 默认为up）
# 请注意，将伺服保持在down位置可能会对电子元件造成压力，不建议在EASY-BRD或ERB板上使用，除非5V电源已经改进，并且在标准ERCF构建中不是必需的。
# 请确保您的硬件适合此任务！
servo_up_angle: 180						# 默认：MG90S伺服：Up=30    ; SAVOX SH0255MG：Up=140
servo_down_angle: 0						# 默认：MG90S伺服：Down=140 ; SAVOX SH0255MG：Down=30
servo_move_angle: 180					# 选择器移动时使用的可选角度（默认为up位置）
servo_duration: 0.2						# 发送到伺服的PWM脉冲的持续时间（自动关闭）
servo_active_down: 0					# 警告：1 = 强制伺服保持在down位置，0 = 移动后释放

# 日志  -----------------------------------------------------------------------------------------------------
# log_level和logfile_level可以设置为以下之一（0 = 基本，1 = 信息，2 = 调试，3 = 跟踪，4 = 开发人员）
# 通常，您可以将控制台日志保持最小，同时仍将调试输出发送到mmu.log文件
# 增加控制台日志级别仅在初始设置期间真正有用，以避免不断打开日志文件、
log_level: 1
log_file_level: 3						# 也可以设置为-1以完全禁用日志文件
log_statistics: 1						# 1以在每次工具更换时记录统计信息（默认值），0以禁用（但仍然记录）
log_visual: 2							# 1记录丝材的可视表示，2压缩形式（默认），0禁用
log_startup_status: 1					# 是否在启动时记录工具到门的状态，1 = 摘要（默认），2 = 完整，0 = 禁用

# 运动速度 -----------------------------------------------------------------------------------------------------------
# 长距离移动比短距离移动快，用于大部分的波登运动。注意，你可以设置两种快速加载速度，具体取决于MMU认为它是从缓冲区还是从卷轴中拉取。通常在从卷轴中拉取时使用较低的速度，因为需要更多的力来克服摩擦，从而防止丢失步进。使用100mm/s速度可能会较"安静"，适用于NEMA14电机或NEMA17薄型电机，但你可以更低以获得更低噪音
# 注意：编码器在超过250mm/s时不能跟上，因此请确保在非常高速度下关闭`bowden_apply_correction`！
gear_from_buffer_speed: 50 #160     	# mm/s 保守值为100mm/s，最大约为350mm/s
gear_from_spool_speed: 50       		# mm/s 在首次从闸门中加载时使用（较低）速度（即从卷轴中拉取）
gear_short_move_speed: 50       		# mm/s 保守值为35mm/s，最大约为100mm/s
gear_homing_speed: 50           		# mm/s 齿轮步进电机仅用于归位移动（例如挤出机归位）

# 挤出机移动速度。当齿轮和挤出机步进电机同步移动时将使用“同步”速度
extruder_load_speed: 15         		# mm/s 从归位位置到熔融区内挤出机的加载移动速度
extruder_unload_speed: 20       		# mm/s 挤出机内卸载移动速度（熔融区内的最初移动为此速度的50%）
extruder_sync_load_speed: 20    		# mm/s 同步挤出机加载移动速度
extruder_sync_unload_speed: 25  		# mm/s 同步挤出机卸载移动速度
extruder_homing_speed: 20       		# mm/s 仅用于挤出机归位移动的速度（例如到工具头传感器）

# 选择器移动速度
selector_move_speed: 200        		# mm/s 选择器移动速度（非触摸）
selector_homing_speed: 60       		# mm/s 初始选择器归位移动速度（非触摸）
selector_touch_speed: 80        		# mm/s 所有触摸选择器移动的速度（如果已配置stallguard）
selector_touch_enable: 0        		# 如果选择器触摸操作可能被禁用，此选项可用于禁用它，1=启用，0=禁用

# 编码器加载/卸载 ---------------------------------------------------------------------------------------------------
# 这些设置控制在闸门中加载和卸载丝杆的可选编码器
encoder_unload_buffer: 50       		# 减小快速卸载的量，以使精确的编码器卸载有足够的空间进行操作
encoder_load_retries: 2         		# MMU尝试在初始加载时抓取丝杆的次数（最大为5）
encoder_parking_distance: 30			# 高级选项：如果指定，控制在闸门中的停车位置（距离编码器的距离，范围=12-30）

# 波登管装载/卸载 --------------------------------------------------------------------------------------------
# 除了不同的波登装载速度适用于缓冲和非缓冲的丝材外，还可以检测到由于"急刹车"而引起的步进电机丢步问题。
# 如果启用波登校正，驱动器将相信编码器读数并进行校正移动，以将丝材移动到距离波登位置末端的 'load_bowden_tolerance' 内
# （这需要可靠的编码器，并且不建议在非常高的加载速度 >200mm/s下使用）
bowden_apply_correction: 0				# 1 启用，0 禁用（默认）
bowden_load_tolerance: 20.0				# 校正移动尝试接近目标的最近距离（以毫米为单位）
bowden_num_moves: 1						# 在装载或卸载波登时要进行的快速移动的次数（如果有TTC错误，则可以大于1）

# 挤出机入口检测/归位 ---------------------------------------------------------------------------------------
# 如果不使用工具传感器（归位端点），驱动器可以通过与挤出机齿轮碰撞来"感知"其进入，并因此需要知道尝试归位的最远距离。
# 由于这种方法不是完全确定的，您可能需要通过调整TMC电流减小来找到您的设置的最佳效果。
# 此外，可以配置触摸（stallguard）感测，但不幸的是与外部EASY-BRD或ERB mcu的兼容性不佳。
# 在碰撞检测期间减小电流还可以防止丝材磨损。
extruder_homing_max: 50					# 尝试归位挤出机时最大前进距离
extruder_homing_endstop: collision		# 丝材归位方法/端点名称（"mmu_gear_touch" 用于 stallguard）或 "collision"
extruder_homing_current: 40				# 在归位挤出机时使用的挤出机电流（10%-100%）（100 禁用）

# 在没有工具传感器的情况下，Happy Hare将自动默认为挤出机入口检测，无论此设置如何，
# 但如果您有工具传感器，您仍然可以强制执行额外的（不必要且不建议的）步骤，即首先归位到挤出机入口，
# 然后再归位到工具传感器。
extruder_force_homing: 0


# 内置默认的工具头加载和卸载序列 -------------------------------------------------------------------------
# 可以定义高度定制的加载和卸载序列，但是除非您有专门的设置，否则选择内置的工具头加载和卸载序列可能会更容易，因为它已经提供了高度的定制性。
# 如果您需要更多控制，请编辑mmu_software.cfg中的_MMU_LOAD_SEQUENCE和__MMU_UNLOAD_SEQUENCE宏，但请小心！
# MMU必须有一个已知的点位于波登管的末端，以便可以精确地加载挤出机。一般来说，这要么是挤出机入口（由上面的设置控制），要么是通过工具头传感器归位。
# 如果您有工具头传感器，它位于挤出机齿轮之后，驱动程序需要知道最大距离（从波登管末端移动）以尝试归位。
toolhead_homing_max: 40					# 尝试归位到工具头传感器的最大距离

# 一旦确定了归位位置，Happy Hare需要知道到喷嘴的最终移动距离。如果是归位到工具头传感器，这将是从工具头传感器到喷嘴的距离。
# 如果是挤出机归位，这将是从挤出机齿轮到喷嘴的距离。设置适合您的设置的适当参数。
# 可以通过手动将丝杆插入到归位点（挤出机齿轮或工具头传感器）并逐次推进1-2mm，直到开始从喷嘴挤出来来确定这个值。从该距离减去1-2mm以得到这个值。如果您的清洁塔有较大的间隙，增加这个值。如果有斑点，减小这个值。这个值将取决于您的挤出机，热端和喷嘴设置。
# （注意这两者之间的差值表示挤出机到传感器的距离，并用作最终从挤出机卸载的距离。准确的设置可以减少喷头从挤出机退出时的噪音/磨损）
toolhead_extruder_to_nozzle: 22			#72	# 例如，使用挤出机归位的Revo Voron与CW2挤出机
toolhead_sensor_to_nozzle: 12			#62	# 例如，使用工具头传感器归位的Revo Voron与CW2挤出机
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

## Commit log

2023-06-24 删除过大文件
    删除过大文件
    [10x11-拖链-1.stl, 10x11-拖链固定-1.stl, 16号刀臂.stl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]
2023-06-24 新增说明文件
    说明文件
2023-06-24 新增说明文件
    新增说明文件
2023-06-24 新增重力回卷料架
    新增重力回卷料架
    [gravity_spoolholder_base_1x.step, gravity_spoolholder_clip_1x.step, gravity_spoolholder_clip_1x.stl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]
2023-06-24 新增CAD文件
    MOD更新
2023-06-24 修改文件名称进行MOD更新
    修改文件名称进行MOD更新
2023-06-24 更新 readme.md
2023-06-24 删一些文件更改下文件结构
    文件太多了整理中
    [10x11-拖链-1.stl, 10x11-拖链固定-1.stl, 2020_25mm_corner_mount.stl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]
2023-06-24 更新MOD解释
    更新MOD解释
2023-06-24 新增D轴版本，修订BOM表
    新增D轴版本，修订BOM表
    [605垫片.stl, 605柱销.stl, 608柱销x4.stl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]
2023-06-24 更新Bom表
    [BOM表.xlsx]
2023-06-24 修改说明文件
    [ERCF主板底座.SLDPRT, ERCF主板底座.STEP]
2023-06-24 料架更新1.7版本
    [605垫片.stl, 605柱销.stl, 608柱销x4.stl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]
2023-06-24 修改文件名称
    [605垫片.stl, 605柱销.stl, 608柱销x4.stl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]
2023-06-25 修订更新记录
2023-06-25 更新错误文件命名
    [6.3干燥箱盖扣.stl, 6.3干燥箱盖扣2.stl, 6.3盖2.stl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]
2023-06-25 删除 release-drafter.yml
2023-06-25 删除 release.yml
2023-06-26 创建 镂空盖子.3mf
    新增镂空盖子避免切片麻烦
    [镂空盖子.3mf]
2023-06-27 更新电动回卷料架
    [6.3盖2.stl, BOM表.xlsx, BOOM表.xlsx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]
2023-06-27 更新砂纸打磨工具随便下载的
    [cale_TOP.STL, cale_body.STL, vis_M8X15.STL]
2023-06-28 更新TR兔MOD，新增5.8L米桶料架
    [5000中.stl, 5000偏.stl, Axle_remix.STL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]
2023-06-28 更新6.3L电动回卷
    [滚筒上.stl]
2023-06-28 更新V4版电动底座
    [TPU齿轮滚筒下.stl, 滚筒上.stl, 滚筒下.stl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]
2023-06-29 大C文件更新
    更新内容看readme
    [10x11-拖链-1.stl, 10x11-拖链固定-1.stl, 6.3干燥剂盒.stl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]
2023-06-29 更新一个klipper 教程可做参考
2023-07-01 更新被动回卷料架V2.0.更新全套MODV1.2
    [[黑]编码器左.stl, 压杆.stl, 车头H6.stl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]
2023-07-02 更新被动回卷料架V2.1版本完结版
    [轴承支架.stl]
2023-07-02 更新全套TR兔MOD，新增空气净化MOD
    [[黑]编码器右.stl, [黑]编码器左.stl, 底盖1.stl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]
2023-07-02 更新1.4版本全套改装，新增被动回卷料架源文件
    [XH2.54母壳卡扣.stl]
2023-07-02 更新XH2.45 卡扣
    [XH2.54母壳卡扣.stl]
2023-07-05 新增Klippercsreen安装手册-不包含快乐兔
2023-07-05 新增中文快乐兔中文配置
    [ercf_parameters.cfg.txt]
2023-07-06 更新电动回卷PCB
    [TR编码器-切刀V5-编码器BOM.xlsx, 电动回卷PCB座.stl]
2023-07-06 删除不必要早期文件不在做备份留存
    [10x11-拖链-1.stl, 10x11-拖链固定-1.stl, 2020_Mount2-1.stl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]
2023-07-06 更新20L自动回卷料架-葉
    [10x11-拖链-1.stl, 10x11-拖链固定-1.stl, 6.3干燥剂盒.stl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]
2023-07-06 更新20L材料箱购买衔接机购买指南
2023-07-09 新增20L料架适配大料盘
    [!物料清单.xlsx, 605垫片.stl, 605柱销x4.stl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]
2023-07-09 改个名字方便查找
    [!物料清单.xlsx, 605垫片.stl, 605柱销x4.stl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]
2023-07-10 更新V3-TR编码器切刀
    修正原版小文件错误感谢群友踩坑！
    [TCRT_Sensor_Anchor_Centered.stl, TCRT_Sensor_Anchor_Off_Centered.stl, 编码器中孔.stl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]
2023-07-11 新增动态网床使用
2023-07-14 更新20L料架V1版本
    [608柱销x4.stl, 608滑轮传动轮、补偿间隙垫片x12.STL, TPU防滑套x2.stl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]
2023-07-14 大C更新电动回卷
    [BOM.xlsx, BOM表.xlsx, 兔子MOB.cfg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]
2023-07-14 说明文件更新
2023-07-16 新增原版xiao配置文件
    [ercf_hardware -兔子原版.cfg]
2023-07-16 更新原版兔子主板参数避免大家找不到对应的配置文件
    [ercf_hardware -兔子原版.cfg, ercf_hardware.cfg, ercf_parameters.cfg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]
2023-07-17 更新初版安装手册
    保姆式教程初版安装更新中
2023-07-17 更新安装教程增加klipper安装教程，增加屏幕教程不准备添加快乐兔屏幕的了自己更新
2023-07-17 更新V3版安装教程
    主要更新大C编码器切刀方案，大C自身的教程我也没用过所以不做具体解释
2023-07-17 更新PDF文件内部部分错误
2023-07-17 更新TR或是TR兔固定底座-群友政政的回忆
    [ERCF主板底座.SLDPRT, ERCF主板底座.STEP, 支架A-政政的回忆录（342467864）.stl]
2023-07-18 更新达赖垂直料架
2023-07-19 新增四色开源项目衔接由于非TR项目暂不做具体收录
2023-07-19 压缩文件节省空间压缩中
    [Axle_remix.STL, Base_box_x2.stl, Base_lid_x2.stl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]
2023-07-19 压缩较大文件节省空间
    [!物料清单.xlsx, 10x11-拖链-1.stl, 10x11-拖链固定-1.stl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]
2023-07-19 同步最新文件
    [10x11-拖链-1.stl, 10x11-拖链固定-1.stl, 2020_Mount2-1.stl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]
2023-07-19 分卷压缩节省空间
    [10x11-拖链-1.stl, 10x11-拖链固定-1.stl, 6.3干燥剂盒.stl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]
2023-07-21 更新手册内容直避坑指南
2023-07-23 更新V5教程添加组合教程持续更新中
2023-07-23 更新大C2文件，更新安装文档
2023-07-23 日常大佬更新
2023-07-27 更新V6教程，添加兔子板接线图看不懂的随意
2023-07-30 更新TR型材固定-愚人方案V1
    不知道打啥就按照中文意思来，或者这自己打开step兔确认打那个
    [TR-1.SLDPRT, tr支架for voron 5mm厚玻璃 直接打.STL, tr支架for voron 5mm厚玻璃.SLDASM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]
2023-07-30 更新V7安装教程
    初步完成教程，安装的的新的作为教程的TR兔慢慢完成理线吧，理线实在是不想做教程，你们自己来吧！
2023-08-05 更新 20L适配-被动回卷料架R2.1-by冷冷哒-唔，待定-v3.zip
2023-08-08 更新檫料，更新快乐兔V2配置文件
    [client_macros.cfg, mmu.cfg, mmu_ercf_compat.cfg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]
2023-08-10 更新快乐兔V2配置，主要为切刀代码位置由原来的3326换为3310理论上可在打印时正常使用具体结果测试中
2023-08-17 日常更新
2023-08-30 方案可行性确认
2023-08-31 更新V8说明
2023-09-16 更新免费兔子板
2023-09-16 更新个名字
2023-09-16 更新下回卷PY文件
2023-09-16 更新下材料清单
2023-09-16 忘记换行了
2023-09-24 更新开源主板
    [client_macros.cfg, mmu.cfg, mmu_ercf_compat.cfg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]
2023-09-24 更新主板截图
    如果需要零件清单请看readme.md文件
2023-09-24 更新说明文件
2023-09-25 更新5.8L被动回卷
2023-09-29 更新验证2040兔子板
2023-09-29 更新主板及龙头切刀
2023-10-02 更新切刀文件，更新主板
2023-10-09 RP2040-zero主板更新测试打板
2023-10-09 微调2040主板电路，完成can板信号输出
2023-10-09 微调走线
2023-10-14 更新兔子主板
    添加
    BOM表及焊接辅助
2023-10-14 过孔问题略微更新
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2023-10-21 更新下最新的配置文件
    [client_macros.cfg, mmu_ercf_compat.cfg, mmu_hardware.cfg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]
2023-10-21 完善配置修正文件名称
    [client_macros.cfg, ercf_hardware.cfg, ercf_parameters.cfg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]
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2023-10-24 添加xiao丝印解决引脚问题看不懂怎么插的自己查英文
2023-10-28 更新通道MOD，送料问题处理
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2023-11-07 更新参数
    [client_macros.cfg, mmu_ercf_compat.cfg, mmu_hardware.cfg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]
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2023-11-15 更新文件中
    [VORON2.4_Assembly_Z Bearing Block Bottom (3) v1.stl, client_macros.cfg, mmu.cfg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]
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2023-12-02 更新文件
    [BOM of 398encoder.xlsx, sx398编码器 滑车+切刀适配beta.STEP]
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2024-05-11 开源1.6.2兔子板
    [Base+1.stl, Base+2.stl, Base+3.stl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]
2024-05-11 删除多余文件-切刀文件需修改
    [Base+1.stl, Base+2.stl, Base+3.stl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]
2024-05-11 删除多余文件-找不到维护方
    [BOM of 398encoder.xlsx, sx398编码器 滑车+切刀适配beta.STEP, wipehole.STEP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]
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2024-09-01 电源板故障，优化修复
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2024-11-21 修改文件及添加花总开源回卷
    花总开源回卷BOM存在缺失暂未补全
    [config.cfg, fortify.cfg]
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2025-03-05 花总主板更新
    [BOM_合宙-RP2040-花满楼定制_花总定制_2024-11-17.xlsx]
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2025-10-14 Create mmu_check_tools_start.cfg
    自定义优化代码增加
    [mmu_check_tools_start.cfg]
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
